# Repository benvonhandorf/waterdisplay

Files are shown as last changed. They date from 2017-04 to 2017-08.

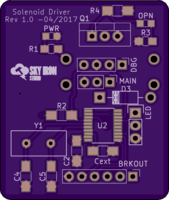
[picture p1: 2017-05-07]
Solenoid Driver Board/Images/v1_0/oshpark-render-front.png

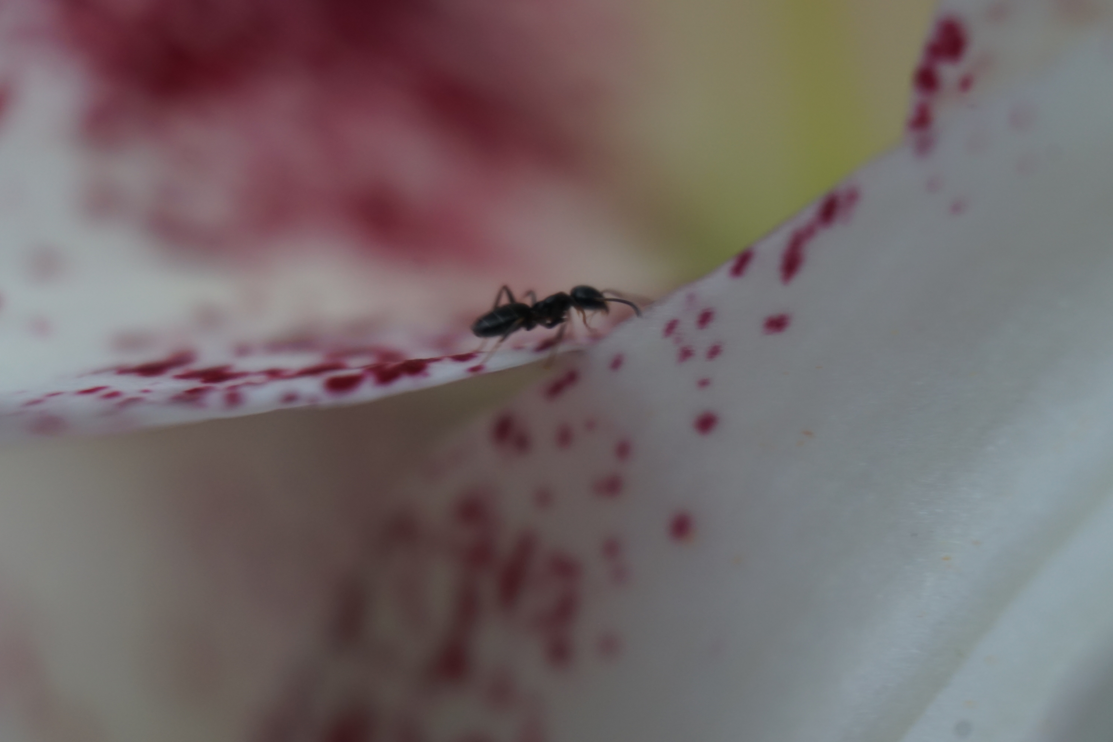
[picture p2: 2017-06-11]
display_playground/source_image.jpg

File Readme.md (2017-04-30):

# Overview

Water Display is intended to be an open source project combining electronics, embedded software and water to create a small water display for our small pond.

# Project goals

As with any project, there are multiple goals here, both primary and secondary

## Primary
* Functional, programmable water display.
* Further my knowledge of electronics.
* Gain some experience circuit board design, using KiCad.

## Secondary
* Minimize cost.  In particular, cost per node should be kept as low as possible.
* Maximize flexibility.  Creating an extensible design capable of doing other tasks in the future would be optimal.
* Learn a new microcontroller, if the opportunity presents itself.

# Design Philosophy

The goal is to have multiple small independent water squirters (a _node_) located around the pond.  Each of these will contain:
* (A small 12V solenoid)[https://www.sciplus.com/p/12-VDC-SOLENOID-VALVE-10PACK-SAVINGS_54414]
* RGB LED
  * WS2812 seems likely
  * APA102 would also work and we have no shortage of GPIO in the node (see below)

These will be run from a central controller running various patterns which could be based on sensors or some other option.

# Component selection

## General

As part of the goal to do circuit board design, most components will be sourced as SMD, where possible.  A few power components will be through hole (e.g. MOSFET, flyback diode) just to give a ridiculous amount of rating overhead.

## Node design

After consideration, I've decided to pursue making each node smart.  This minimizes the required bus lines, maximizes the expandability of the installation and hopefully allows for different use cases for the electronic work.

Intended communication is over a shared serial UART from the controller to all nodes.  Each node will have an address assigned to it (compiled in to the flash) and the protocol will allow it to only process messages intended for it.

To further reduce cabling requirements, each node will have a local 5V regulator for Vdd supply for the microcontroller and RGB LED.

### Microcontroller

General Requirements:
* UART
* 5V part (to eliminate the need for further regulation)
* At least 3 GPIO pins
  * MOSFET
  * LED Data
  * LED Clock, if an APA102 style RGB LED is used

In order to keep cost per part down and given the very modest requirements above, an STM8 type part is recommended.  Research indicates they can be sourced at less than $0.50/pc in small quantities.  Given the small amount of board space available (with an optimally sized circuit board) and the need to hand-solder the parts, a TSSOP20 part is suggested.  RAM and Flash requirements should be very modest, to a STM8S003F or similar part should be sufficient in all respects.  Even if I decided to make a 4-way node, there should still be sufficient GPIO available.

Given the lack of additional requirements, where possible GPIO pins should be selected to maximize future expandability.  SPI and I2C should be left available, if possible, along with ADC pins.  

#### Microcontroller supporting parts

* 1 uF ceramic capacitor - Power smoothing Capacitor 
* Cext - 1 uf
  * 0.3 Ohm Max ESR at 1MHz 
  * 15 nH Max ESL at 1MHz
* If an external oscillator is necessary:
  * 16 MHz crystal
  * 2 x 20pF Load capacitors, depending on Cload

### Connectivity

Connections from central node are:
* +12V DC
* 0V DC
* Serial Data (TX from controller)
* Pressurized water (obviously.  Solenoid ratings call for < 4psi)

Additional local connections for programming and debugging (not exposed through weatherproof casing)
* Serial Data (TX from node)
* Reset
* SWIM
* +5VDC
* Ground

### Additional

In order to make the design as maintainable as possible, the following indicator LEDs will be placed on the board as well:
* Green power indicator LED, connected to 12V line
* Red "active" LED, connected to MOSFET control pin

# BOM
## Per Node BOM
* Microcontroller
  * STM8S003F ~ $0.50/pc
  * STM8S103F ~ $0.50/pc
  * MSP430G2001 ~ $0.
* AMS1117 ~ $0.10/pc
* 2x female spade connectors ~ $0.28/pc (e.g. 1217080-1)[http://www.newark.com/webapp/wcs/stores/servlet/ProductDisplay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]
*

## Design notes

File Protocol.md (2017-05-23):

# Purpose

This protocol is designed to be used for the controller to node communication in the water display.  Limitations will primarily be driven by the nodes, since they are the more processor limited side of the communication.

Note that this is not intended to limit the TX side from the individual nodes, which will be primarily used for debugging and should be free to speak whatever is most useful.

# Serial Communication Settings

For the development state at least, communication will be at 9600 N-8-1 to allow for easiest debugging.  If this results in too much lag in reality higher baud rates will be used.

# Node Addressing

The STM8 supports inherently dealing with node addressing by using Address Mark Detection (See reference manual, page 334).  The MSB of the first byte in the Address byte must be 1 and the 4 LSBs will be compared with the ADD bits in UART_CR4.  This un-mutes that receiver until a different address byte is received.  This allows the possibility of transmitting multiple commands without re-addressing the node.

A limitation of this approach is that there is no support for broadcast packets.  This may wind up being an issue for large coordinated changes of many nodes at once.  If so, this can either be addressed by increased transmission speeds or by revisiting the mute mode used (or not using any mute mode at all).

# General Protocol Design

## Limitations

Due to the addressing mode choices above, non-address bytes may not have their MSB set.  This limits us to bytes between 0x00 and 0x7F for commands and data.  Addresses bytes will be between 0x80 and 0x8F, limiting the network to 16 nodes with this version of the protocol.  Future versions not using the address muting of the STM8 may be able to use up to 127 nodes without violating the MSB

To allow expandability of the network, some consideration must be given to message compactness while still hopefully allowing for node growth and enhanced capabilities (e.g. multiple sprayers and LEDs).

## Node Addressing

A node will be muted, listening only until its address byte is seen.  After a node is addressed it will continue to listen to commands until another node is addressed, at which point it will enter mute mode again.

## Command Structure

Generally a command will be followed by 0-n data bytes defining some aspect of the behavior.

### General Commands

#### Command: `D`
Data Bytes: 0

##### Meaning
Dump current state to TX pin.  The node should output its current internal state and any useful debugging information to the serial interface.  The format of this data should be as human readable as possible but does not have any defined requirements.

#### Command: `F`
Data Bytes: 0

##### Meaning
Off.  Shut down all peripherals on the node.  Solenoids should be de-energized, LEDs should be turned off.

### Solenoid Commands

#### Command: `S`
Data Bytes: 1

##### Meaning
Set solenoids to the specified state, with 0 representing de-energized and 1 representing energized.  Each solenoid on a sprayer will be represented by a single bit, so up to 8 solenoids are supported by a single node using this command.

### LED Commands

#### Command: `L`
Data Bytes: 1 Count Byte followed by (4 * Count) data bytes.
Each set of 4 data bytes shall be in R G B W order and represent a *Color Packet*.

##### Meaning
Set LEDs to a specific RGBW code, instantaneously.  For nodes with multiple LEDs the first *Color Packet* should correspond with the LSB solenoid, to the extend possible.  Subsequent color packets should correspond to more significant solenoids, as makes sense.

Since each color byte must NOT have the MSB set, each byte should be right shifted by 1 by the transmitter and left shifted by 1 by the receiver.  This results in a loss of 1 bit of accuracy for each channel, but given the general limitations of RGB LEDs this should be fairly acceptable.

There is no assumption that the number of LEDs is equal to the number of solenoids, just that their physical direction corresponds roughly when appropriate.

For nodes speaking to hardware with non R G B W color order of bytes, it is reliant upon the node to handle the appropriate re-ordering of bits.  For nodes with no white channel on their LED, they should ignore the W byte.  In a case where no W channel is available the node MAY make an attempt to emulate it by changing the R G B channel values to use a simulated white.  No allowance is made for different white color temperatures.

#### Command: `l`
Data Bytes: 1 duration byte (max 127), 1 Count Byte (max 127) followed by (4 * Count) data bytes.
Each set of 4 data bytes shall be in R G B W order and represent a *Color Packet*.

##### Meaning
Fade LEDs to a specific RGB code.  First byte represents 50ms increments to use for fade duration, all subsequent bytes are as `L`

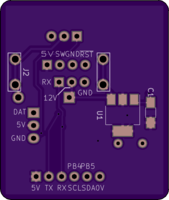
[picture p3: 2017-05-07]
Solenoid Driver Board/Images/v1_0/oshpark-render-back.png

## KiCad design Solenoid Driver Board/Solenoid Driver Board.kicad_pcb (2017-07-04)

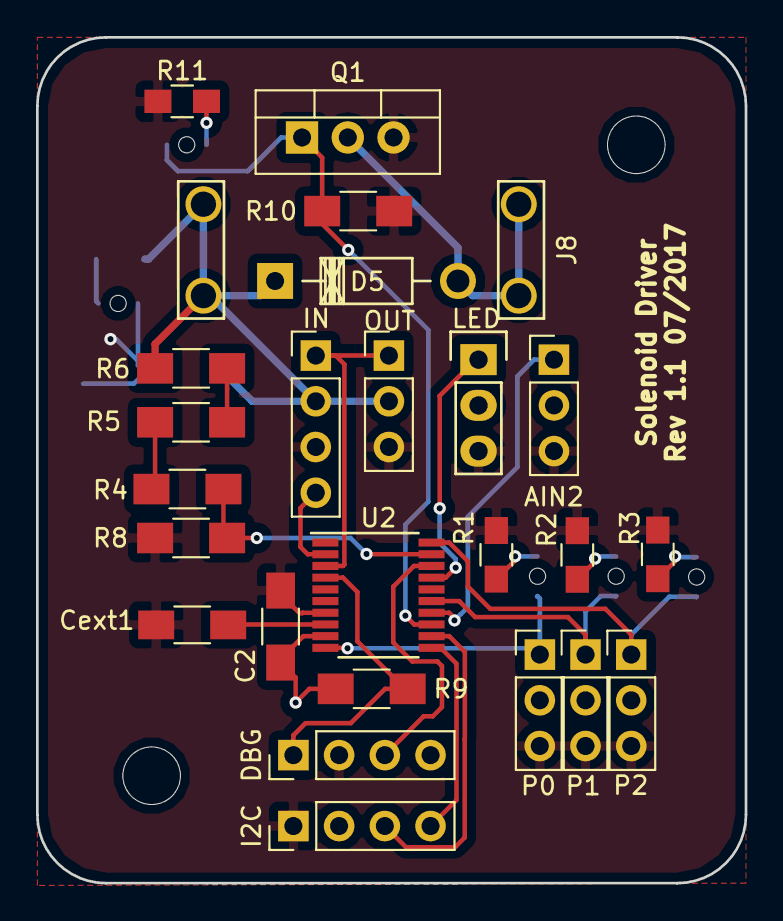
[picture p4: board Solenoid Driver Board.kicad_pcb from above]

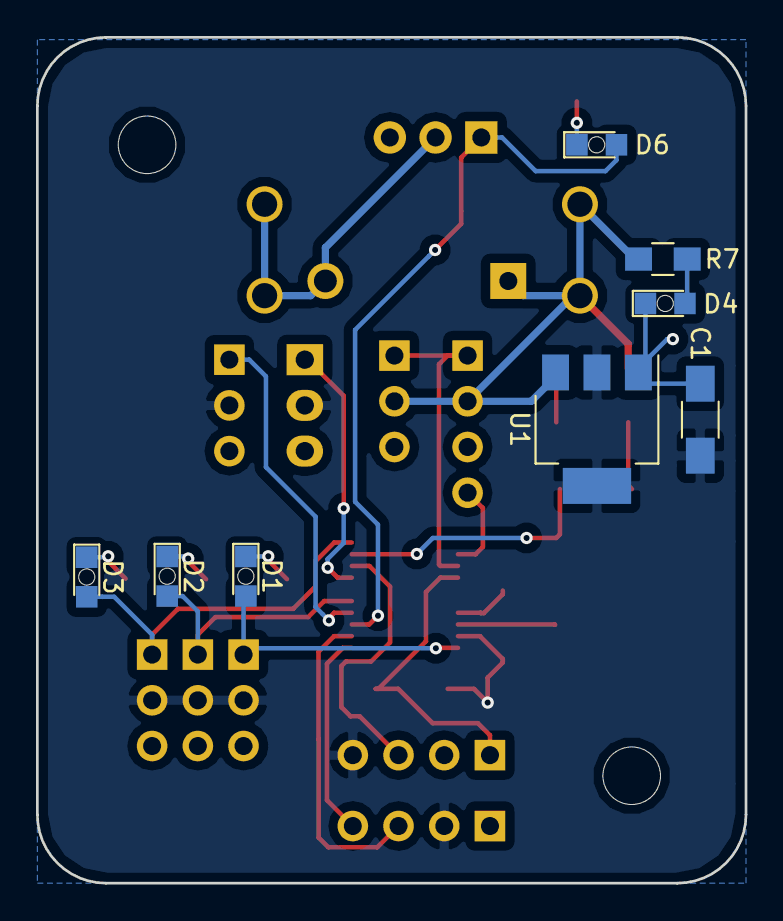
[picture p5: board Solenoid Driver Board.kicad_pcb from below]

Board: 2 copper layers, 39.4 x 47.0 mm, 33 parts (8 on the bottom side), 25 nets.

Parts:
AIN2: AIN2; Pin_Header_Straight_1x03_Pitch2.54mm
C1: 1 uF; C_1206_HandSoldering
C2: 100nf; C_1206_HandSoldering
Cext1: 1 uF; C_1206_HandSoldering
D1, D2, D3, D6: ON; LED_0805_Bottom_Hole
D4: PWR; LED_0805_Bottom_Hole
D5: 1N4007; Diode_DO-41_SOD81_Horizontal_RM10
DBG: DEBUG; Pin_Header_Straight_1x04_Pitch2.54mm
I2C: I2C; Pin_Header_Straight_1x04_Pitch2.54mm
IN: BUS-I; Pin_Header_Straight_1x04_Pitch2.54mm
J8: Solenoid; Spade_Conn_Solenoid
LED: RGB_LED; Pin_Header_Straight_1x03
OUT: BUS-O; Pin_Header_Straight_1x03_Pitch2.54mm
P0: CH1; Pin_Header_Straight_1x03_Pitch2.54mm
P1: CH2; Pin_Header_Straight_1x03_Pitch2.54mm
P2: CH3; Pin_Header_Straight_1x03_Pitch2.54mm
Q1: IRLB8721PBF; TO-220_Vertical
R1, R2, R3, R11: 330; R_0805_HandSoldering
R4, R5, R6, R8, R9: 10k; R_1206_HandSoldering
R7: 1k; R_0805_HandSoldering
R10: 10K; R_1206_HandSoldering
U1: AMS1117-5.0; SOT-223
U2: STM8S003F3P; TSSOP-20_4.4x6.5mm_Pitch0.65mm

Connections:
+5V: AIN2.2, C1.1, C2.1, DBG.4, I2C.2, LED.2, P0.2, P1.2, P2.2, R9.1, U1.2, U1.4, U2.9
+12V: D5.1, IN.2, J8.1, OUT.2, R6.1, R7.1, U1.3
AIN2: AIN2.1, U2.14
CH0: D1.2, P0.1, U2.10
CH1: D2.2, P1.1, U2.15
CH2: D3.2, P2.1, U2.20
GND: AIN2.3, C1.2, C2.2, Cext1.2, D4.1, DBG.2, I2C.1, IN.3, LED.3, OUT.3, P0.3, P1.3, P2.3, Q1.3, R1.1, R2.1, R3.1, R8.1, R10.1, R11.1, U1.1, U2.7
NRST: DBG.1, R9.2, U2.4
unnamed: Cext1.1, U2.8
unnamed: D1.1, R1.2
unnamed: D2.1, R2.2
unnamed: D3.1, R3.2
unnamed: D4.2, R7.2
unnamed: D5.2, J8.2, Q1.2
unnamed: D6.1, R11.2
unnamed: LED.1, U2.17
unnamed: R4.1, R5.1
unnamed: R5.2, R6.2
PC3: D6.2, Q1.1, R10.2, U2.13
RX: IN.1, OUT.1, U2.3
SCL: I2C.3, U2.12
SDA: I2C.4, U2.11
SWIM: DBG.3, U2.18
TX: IN.4, U2.2
VIN_A: R4.2, R8.2, U2.19

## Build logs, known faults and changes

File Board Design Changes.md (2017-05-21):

# Post v1.0

* Align indicator LEDs
* Break out more pins using another header + push and shove router
* Break out PWM/Timer pins specifically
* Use a daisy-chain topology to send serial in, +12V and GND back out on another header

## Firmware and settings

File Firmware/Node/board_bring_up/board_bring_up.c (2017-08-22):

#include <stdint.h>
#include "stm8s.h"
#include "stm_util.h"

volatile uint8_t state = 0;
volatile uint8_t timer_counter = 0;
volatile uint8_t pwm_cycle = 0;

void tim4_isr(void) __interrupt(TIM4_vector) {
  if(TIM4_SR & TIM_SR1_UIF){
    timer_counter++;
    if(timer_counter % 10 ==0) {
      pwm_cycle++;
    }
    if(timer_counter == 50) {
      timer_counter = 0;
      state++;
    }
    CLRBIT(TIM4_SR, TIM_SR1_UIF);
  }
}

void tim4_init() {
  //Targeting a 50ms timer
  TIM4_PSCR = 0x07; //Prescaler = 128

  SETBIT(TIM4_IER, TIM_IER_UIE);
  SETBIT(TIM4_CR1, TIM_CR1_CEN);
}

void tim2_init() {
  TIM2_PSCR = 0x03; //Prescaler

  TIM2_ARRH = 0x00;
  TIM2_ARRL = 0xFF;

  TIM2_CCMR1 = 0x68; //PWM Mode 111, Preload register enabled

  TIM2_CCR1H = 0x00;
  TIM2_CCR1L = 0xFF;

  TIM2_CCMR2 = 0x78; //PWM Mode 111, Preload register enabled

  TIM2_CCR2H = 0x00;
  TIM2_CCR2L = 0x80;

  TIM2_CCMR3 = 0x78; //PWM Mode 111, Preload register enabled

  TIM2_CCR3H = 0x00;
  TIM2_CCR3L = 0x7F;

  TIM2_CCER1 = 0x01 | 0x10; //CC1 and 2 enabled
  TIM2_CCER2 = 0x01; //CC3 enabled



  SETBIT(TIM2_CR1, 0x80);
  SETBIT(TIM2_CR1, TIM_CR1_CEN);
}

void main() {

  smi();

  CLK_DIVR = 0x00;
  CLK_PCKENR1 = 0xFF;

  //Main Control 
  SETBIT(PC_DDR, 0x08);
  SETBIT(PC_CR1, 0x08);
  CLRBIT(PC_ODR, 0x08);

  tim4_init();
  tim2_init();

  rmi();  

  while(1) {
    //Main Control 
    CLRBIT(PC_ODR, 0x08);

    TIM2_CCR1H = 0x00;
    TIM2_CCR1L = pwm_cycle;

    TIM2_CCR2H = 0x00;
    TIM2_CCR2L = pwm_cycle;

    TIM2_CCR3H = 0x00;
    TIM2_CCR3L = pwm_cycle;

    if((state + 0) % 4 == 3) {
      // Main Control 
      SETBIT(PC_ODR, 0x08);
    }
  }
}

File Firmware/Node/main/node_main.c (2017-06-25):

#include <stdint.h>
#include "stm8s.h"
#include "stm_util.h"
#include "uart_driver.h"
#include "solenoid_driver.h"
#include "led_driver.h"
#include "controller.h"
#include "configuration.h"
#include "status_driver.h"

#ifndef DEFAULT_NODE_ADDRESS
#define DEFAULT_NODE_ADDRESS 0x01
#endif

volatile uint8_t fade_cycles = 0;
volatile uint8_t timer_counter = 0;

void uart1_tx_isr_handler(void) __interrupt(UART1_TXE_vector) {
  uart1_tx_isr();
}

void uart1_rx_isr_handler(void) __interrupt(UART1_RXF_vector) {
  uart1_rx_isr();
}

void tim4_isr(void) __interrupt(TIM4_vector) {
  if(TIM4_SR & TIM_SR1_UIF){
    timer_counter++;
    if(timer_counter == 25) {
      timer_counter = 0;
      fade_cycles++;
    }
    CLRBIT(TIM4_SR, TIM_SR1_UIF);
  }
}

void tim4_init() {
  //Targeting a 50ms timer
  TIM4_PSCR = 0x07; //Prescaler = 128

  SETBIT(TIM4_IER, TIM_IER_UIE);
  SETBIT(TIM4_CR1, TIM_CR1_CEN);
}

uint8_t RED[] = {0xFF, 0x00, 0x00, 0x00, 0xFF, 0x00, 0x00, 0x00};

void main() {
  char buffer[32];
  uint8_t bytesReceived = 0;
  uint8_t nodeAddress = configuration_get(CNF_ADDR);

  smi();

  CLK_DIVR = 0x00;
  CLK_PCKENR1 = 0xFF;

  if(nodeAddress == 0
    || nodeAddress > 0x0F) {
    nodeAddress = DEFAULT_NODE_ADDRESS;
  }
  
  uart_init(nodeAddress);
  solenoid_init();
  led_init(1);
  controller_init();
  status_init();

  tim4_init();

  IWDG_KR = 0xCC;
  IWDG_PR = 0x02;

  rmi();  

  status_set(STATUS_ONE);

  while(1) {
    uint8_t i ;
    int bytesReceived = uart_read(buffer, 32);
    controller_add_bytes(buffer, bytesReceived);

    for(i = 0; i < fade_cycles; i++) {
       led_fade();
    }

    IWDG_KR = 0xAA;

    fade_cycles = 0;

    if(bytesReceived) {
      status_set(STATUS_ONE);
    } else {
      status_clear(STATUS_ONE);
    }
  }
}

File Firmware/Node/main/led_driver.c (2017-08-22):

#include <stdint.h>
#include <stdlib.h>
#include <string.h>
#include "led_driver.h"

#if 0

#include "pl9823_driver.h"

void(*impl_init)() = &pl9823_init;
void(*impl_write)(uint8_t *) = &pl9823_write_led;
void(*impl_latch)() = &pl9823_latch;

#else

#include "pwm_led_driver.h"

void(*impl_init)() = &pwmled_init;
void(*impl_write)(uint8_t *) = &pwmled_write_led;
void(*impl_latch)() = &pwmled_latch;

#endif

#define min(a, b) (a > b ? b : a)

uint8_t OFF[] = {0x00, 0x00, 0x00, 0x00};

uint8_t ledCount;
LED_DATA_T *ledData = NULL;
FADE_DATA_T fadeData;

void led_send_string() {
  uint8_t i;

  for(i = 0; i < ledCount; i++) {
    LED_DATA_T *led = ledData + i;

    uint8_t *bytes = led->current;
    impl_write(bytes);
  }

  impl_latch(); 
}

void led_init(uint8_t led_count) {
  ledCount = led_count;

  ledData = (LED_DATA_T *) malloc(sizeof(LED_DATA_T) * ledCount);

  fadeData.fadeTotal = 0;
  fadeData.fadeComplete = 0;

  impl_init();

  impl_latch(); 

  led_off();
}

#define FADEVAL(sourceValue, targetValue, portion) (uint8_t) (sourceValue + ((((uint16_t) targetValue) - sourceValue) *portion )/255)

void led_fade_single(LED_DATA_T * led, uint8_t fadePortion) {
    led->current[0] = FADEVAL(led->source[0], led->target[0], fadePortion);
    led->current[1] = FADEVAL(led->source[1], led->target[1], fadePortion);
    led->current[2] = FADEVAL(led->source[2], led->target[2], fadePortion);
    led->current[3] = FADEVAL(led->source[3], led->target[3], fadePortion);
}

void led_fade() {
  uint8_t fadePortion;
  uint8_t i ;

  if(fadeData.fadeTotal == 0) {
    return;
  }

  fadeData.fadeComplete += 1; //Expect this to be called every ~50 ms

  fadePortion = (((uint16_t) fadeData.fadeComplete) * 255) / fadeData.fadeTotal;

  if(fadeData.fadeComplete >= fadeData.fadeTotal) {
    fadeData.fadeTotal = 0;
    for(i = 0 ; i < ledCount; i++) {
      LED_DATA_T *led = ledData + i;
      
      memcpy(&led->current, &led->target, 4);
    }
  } else {
    for(i = 0 ; i < ledCount; i++) {
      LED_DATA_T *led = ledData + i;

      led_fade_single(led, fadePortion);
    }
  }

  led_send_string();
}

void led_write_values(uint8_t leds, uint8_t *led_bytes) {
  uint8_t i;

  leds = min(leds, ledCount);
  
  for(i = 0 ; i < leds ; i++) {
    uint8_t *bytes = led_bytes + (4 * i);
    LED_DATA_T *led = ledData + i;
    memcpy(&led->current, bytes, 4);
  }

  fadeData.fadeTotal = 0;
  led_send_string();
}

void led_write_fade_target(uint8_t fade_cycles, uint8_t leds, uint8_t *led_bytes) {
  uint8_t i;
  
  leds = min(leds, ledCount);

  for(i = 0 ; i < leds ; i++) {
    uint8_t *bytes = led_bytes + (4 * i);
    LED_DATA_T *led = ledData + i;

    memcpy(&led->source, &led->current, 4);
    memcpy(&led->target, bytes, 4);
  }

  fadeData.fadeTotal = fade_cycles;
  fadeData.fadeComplete = 0;
  led_fade();
}

void led_off() {
  uint8_t i;
  for(i = 0 ; i < ledCount ; i++) {
    LED_DATA_T *led = ledData + i;
    memcpy(&led->current, OFF, 4);
  }

  fadeData.fadeTotal = 0;
  led_send_string();
}

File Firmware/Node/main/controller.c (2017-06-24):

#include <stdint.h>
#include <stdio.h> 
#include <string.h>
#include "controller.h"
#include "solenoid_driver.h"
#include "led_driver.h"
#include "circular_buffer.h"
#include "uart_driver.h"
#include "configuration.h" 
#include "status_driver.h"

#ifndef FIRMWARE_VERSION
#define FIRMWARE_VERSION "0.0.3"
#endif

extern uint8_t ledCount;
extern LED_DATA_T *ledData;
extern FADE_DATA_T fadeData;

CIRCULAR_BUFFER commandBuffer ;

void controller_ack(char cmd) {
  uart_write("ACK-", 4);
  uart_write(&cmd, 1);
  uart_write("\n",1);
}


void controller_dump_state() {
  char buffer[10];
  uart_write("V:", 2);
  uart_write(FIRMWARE_VERSION, strlen(FIRMWARE_VERSION));
  uart_write("\n", 1);
  sprintf(buffer, "A:%2x\n", uart_address());
  uart_write(buffer, strlen(buffer));
  sprintf(buffer, "S:%2x\n", solenoid_state());
  uart_write(buffer, strlen(buffer));
  sprintf(buffer, "L:%u\n", ledCount);
  uart_write(buffer, strlen(buffer));
  if(ledCount > 0) {
    sprintf(buffer, "E:%02x%02x%02x\n", ledData[0].current[0], ledData[0].current[1], ledData[0].current[2]);
    uart_write(buffer, strlen(buffer));
  }
}

void controller_init() {
  buffer_init(&commandBuffer);

  controller_dump_state();
}

uint8_t parseBuffer[32];
void controller_off() {
  solenoid_write(0x00);
  led_off();
}

uint8_t controller_D(uint8_t *commandBuffer, uint8_t availableBytes) {
  int bytes_required = 1;
  if(availableBytes >= bytes_required) {
    controller_dump_state();

    controller_ack('D');

    return bytes_required;
  } else {
    return 0;
  }
}

uint8_t controller_A(uint8_t *commandBuffer, uint8_t availableBytes) {
  int bytes_required = 2;
  if(availableBytes >= bytes_required) {
    uint8_t proposedAddress = commandBuffer[1] ;

    if(proposedAddress == 0
      || proposedAddress > 0x0F) {
      uart_write("Invalid address\n", 16);
    } else {
      proposedAddress = configuration_set(CNF_ADDR, proposedAddress);
      uart_write("New Addr: ", 10);
      uart_write(&proposedAddress, 1);
      uart_write("\n", 1);
      controller_ack('A');
    }

    return bytes_required;
  } else {
    return 0;
  }
}

uint8_t controller_F(uint8_t *commandBuffer, uint8_t availableBytes) {
  int bytes_required = 1;
  if(availableBytes >= bytes_required) {
    controller_off();

    controller_ack('F');

    return bytes_required;
  } else {
    return 0;
  }
}

uint8_t controller_S(uint8_t *commandBuffer, uint8_t availableBytes) {
  int bytes_required = 2;
  if(availableBytes >= bytes_required) {
    uint8_t solenoidCommand ;

    solenoidCommand = commandBuffer[1];

    solenoid_write(solenoidCommand);

    controller_ack('S');

    return bytes_required;
  } else {
    return 0;
  }
}

uint8_t controller_L(uint8_t *commandBuffer, uint8_t availableBytes) {
  int bytes_required = 2; //Minimum
  int leds = 1; //Minimum
  int led_offset = 2;
  if(availableBytes >= bytes_required) {
    leds = *(commandBuffer+1);

    bytes_required = led_offset + (4 * leds);
  }

  if(availableBytes >= bytes_required) {
    uint8_t i = 0;

    for(i = led_offset ; i < bytes_required; i++ ) {
      //Left shift bytes of LED data by 1 bit to handle MSB issues.
      commandBuffer[i] = commandBuffer[i] << 1;
    }    

    led_write_values(leds, commandBuffer + led_offset);

    controller_ack('L');

    return bytes_required;
  } else {
    return 0;
  }
}

uint8_t controller_l(uint8_t *commandBuffer, uint8_t availableBytes) {
  int bytes_required = 3; //Minimum
  int leds = 1; //Minimum
  int led_offset = 3;
  if(availableBytes >= bytes_required) {
    leds = commandBuffer[2];

    bytes_required = led_offset + (4 * leds);
  }

  if(availableBytes >= bytes_required) {
    uint8_t i = 0;
    uint8_t delay = commandBuffer[1];

    for(i = led_offset ; i < bytes_required; i++ ) {
      //Left shift bytes of LED data by 1 bit to handle MSB issues.
      commandBuffer[i] = commandBuffer[i] << 1;
    }    

    led_write_fade_target(delay, leds, commandBuffer + led_offset);

    controller_ack('l');

    return bytes_required;
  } else {
    return 0;
  }
}

void controller_add_bytes(uint8_t *bytes, uint8_t length) {
  uint8_t availableBytes;
  uint8_t continueParsing = 1;
  buffer_copy_from(&commandBuffer, bytes, length);

  availableBytes = buffer_bytes(&commandBuffer);

  status_set(STATUS_TWO);

  if(availableBytes > 0) {
    uint8_t *commandStart = parseBuffer;
    availableBytes = buffer_copy_to(&commandBuffer, parseBuffer, 32);

    while(availableBytes > 0 && continueParsing) {
      uint8_t leds = 1; //We will have AT LEAST 1 LED for any LED command
      uint8_t bytes_consumed = 0;

      switch(*commandStart) {
        case 'D':
          bytes_consumed = controller_D(commandStart, availableBytes);
          break;
        case 'F':
          bytes_consumed = controller_F(commandStart, availableBytes);
          break;
        case 'S':
          bytes_consumed = controller_S(commandStart, availableBytes);
          break;
        case 'L':
          bytes_consumed = controller_L(commandStart, availableBytes);
          break;
        case 'l':
          bytes_consumed = controller_l(commandStart, availableBytes);
          break;
        case 'A':
          bytes_consumed = controller_A(commandStart, availableBytes);
          break;
        default:
          //Start of the buffer is a command we don't recognize or a random byte.  We need to move on.
          uart_write("U:", 2);
          uart_write(commandStart, 1);
          uart_write("\n", 1);

          bytes_consumed = 1;

          break;
      }

      if(bytes_consumed > 0) {
        commandStart += bytes_consumed;
        availableBytes -= bytes_consumed;
        buffer_consume(&commandBuffer, bytes_consumed);
        uart_write("N:", 2);
        uart_write(&bytes_consumed, 1);
        uart_write(&availableBytes, 1);
        uart_write("\n", 1);
      } else {
        continueParsing = 0;
      }
    }
  }

  status_clear(STATUS_TWO);
}

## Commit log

2015-03-02 Source for solenoid tests
2015-03-02 Added initial part designs
    [Solenoid Holder - 5 - Partial.stl, Solenoid Holder - Prototype.scad, Solenoid Holder - Prototype.stl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]
2015-03-05 Added support for a compact layout, where alternate solenoids are displaced Y axis.
    + Still possible to make it more compact (along X) by rotating so that feed tubes are on alternating sides.
    [Solenoid Holder - 5 - Partial.stl, Solenoid Holder - Prototype.scad, Solenoid.scad]
2017-04-17 Old changes
    [Solenoid Holder - 5 - Partial.stl, Solenoid Holder - Prototype.scad, Solenoid Holder - Prototype.stl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]
2017-04-18 Restarting the repo
    [Solenoid Driver Board.kicad_pcb, Solenoid Driver Board.sch]
2017-04-18 Documentation work
    [Solenoid Driver Board.sch]
2017-04-18 Cleaned old designs
    [Solenoid Holder - 5 - Partial.stl, Solenoid Holder - Prototype.scad, Solenoid Holder - Prototype.stl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]
2017-04-18 Initial schematic work
    [Solenoid Driver Board.sch]
2017-04-18 Spade connectors added
    [Solenoid Driver Board.sch]
2017-04-30 PCB Design completed and apparently acceptable
    [_saved_Solenoid Driver Board.sch]
2017-05-07 Initial thoughts on protocol. Initial board redesign notes. Added libraries for firmware development
    [Solenoid Driver Board.sch, _saved_Solenoid Driver Board.sch]
2017-05-07 Added oshpark renders of v1.0 of board
2017-05-14 Basic python simulation framework for display creation
2017-05-21 Firmware framework, makefile, board_bring_up tests started
2017-05-21 Circular buffer work for UART
2017-05-21 Circular buffer tests passing, starting work on UART TX code
2017-05-22 UART TX and RX working for basic cases. Still can't stream data to the TX too quickly
2017-05-23 Protocol changes to deal with possible RGBW LEDs, framework for controller and pl9823
2017-05-27 Basic LED fading, not correct yet
    [board_bring_up.c]
2017-05-27 Added unit tests for pl9823 driver
2017-05-27 Refactored hardware PL9823 logic out of general LED driver.
2017-05-27 Fixed LED stand write routine
    [led_driver.c, led_driver_test.c]
2017-05-28 Added LED write and fade interface
2017-05-29 Timer code started but not yet working, UART changed to use address mode
2017-05-29 Clearing timer UIE bit made timer work
2017-05-29 led driver debugging
2017-05-29 Fix bug with led_driver not initting pl9823_driver (mega-DUH)
    [board_bring_up.c, led_driver.c]
2017-05-31 Debugging LED fading issues
    [board_bring_up.c, led_driver.c, led_driver_test.c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]
2017-06-02 Fix reporting of fade colors
    [headless.py]
2017-06-08 Added address configuration to controller and eeprom handling
    [configuration.h]
2017-06-14 Fixing impage parser for use on rpi
    [headless.py, image_parser_program.py]
2017-06-18 Simplified display program to crash node more quickly
    [headless.py, image_parser_program.py, simple_display_program.py]
2017-06-24 Added status drivers, removed batched uart write
2017-06-25 Moved fade to TIM4, started work on new board revision
    [Solenoid Driver Board.kicad_pcb, Solenoid Driver Board.sch, _saved_Solenoid Driver Board.sch]
2017-06-25 Added IWDG timer support
    [Solenoid Driver Board.sch, _saved_Solenoid Driver Board.sch]
2017-06-26 Layout work begun on v1.1 of PCB
    [Solenoid Driver Board.kicad_pcb, Solenoid Driver Board.sch, _saved_Solenoid Driver Board.sch]
2017-06-26 New source image
    [Solenoid Driver Board.kicad_pcb, Solenoid Driver Board.sch]
2017-07-04 PWM Test, lots of work on v1.1 PCBs
    [RPi Voltage Regulator Board.kicad_pcb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]
2017-08-03 Board rev 1.1
    [RPi Voltage Regulator Board-B.Cu.gbr, RPi Voltage Regulator Board-B.Mask.gbr, RPi Voltage Regulator Board-B.SilkS.gbr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]
2017-08-15 Reorganized node firmware
    [configuration.h]
2017-08-22 Switch to correct AFR bit
    [board_bring_up.c, pwm_test.c]
2017-08-22 PWM Working on solenoid board
2017-08-22 PWM driver working, led driver configurable with pound if
